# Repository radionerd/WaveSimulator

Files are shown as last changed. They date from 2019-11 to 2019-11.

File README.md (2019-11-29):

# Ship Motion Simulator

## Welcome

This is the repository for the Ship Motion Simulator design files

The design is contained in these folders:

* firmware   - Arduino .ino source file and status screenshot

* mechanical - LibreCAD drawings and templates - print the templates, glue on to mdf for cutting and drilling

* schematic  - EaglePCB schematics - also provided as pdf

* parts      - A list of all the purchased parts and where to get them

## Arrangement

The motion platform is controlled by an Arduino Nano mounted on the underside.

The Arduino Nano USB serial connection provides optional command line control and a status screen.

An optional plug in control panel provides convenient user controls using switches, potentiometers and a status LED.

## Background

The simulator was designed to approximate the pitch, roll and heave motions of a ship at sea using low cost model control servos.

For a more accurate simulation consider a Stewart Plaform with six degrees of freedom using linear actuators but higher cost and complexity.

The design was built and tested using the following software:

| Application | Version |
| --- | --- |
|  Arduino  | 1.8.9 |
|  EaglePCB | 8.3.1 |
|  LibreCAD | 2.1.2 |
|  Ubuntu | 18.04 |

## Photos and Videos

[Video](https://www.youtube.com/watch?v=MUajh_KlW8U) - Motion Research Ltd

[Construction Photos and Videos](https://photos.app.goo.gl/xF3chL2MP4UncZHGA)

## License

Copyright (C)2019 richard.jones.1952@gmail.com

[License GPL V3.0](https://www.gnu.org/licenses/gpl-3.0.en.html)

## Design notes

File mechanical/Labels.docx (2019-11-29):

Roll

Pitch

Heave

Period

Amplitude

USB USB USB USB

Panel

Auto

Manual

Motion Simulator

5V DC 5V DC

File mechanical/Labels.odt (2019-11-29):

Roll

Pitch

Heave

Period

Amplitude

USB

Panel

Auto

Manual

Motion Simulator

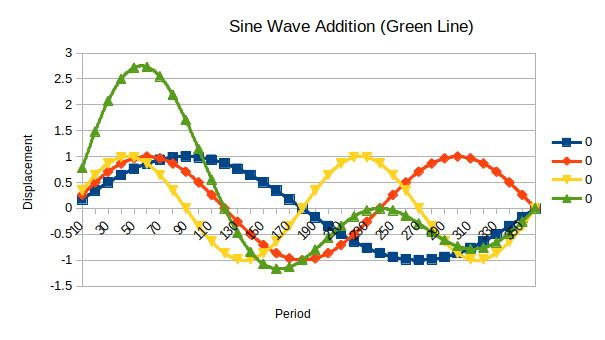
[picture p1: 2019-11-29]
firmware/SineWaveAddition.png

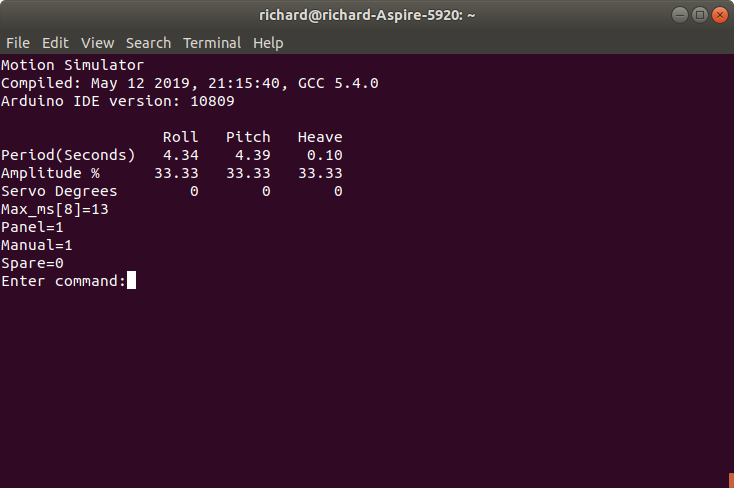
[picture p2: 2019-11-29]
firmware/Screenshot.png

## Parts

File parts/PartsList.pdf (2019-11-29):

### Sheet1

TotCost US$ | Cost NZ$ Order Qty | Description
2.56 USD | $3.97 Qty 2 ✔ | 20 way idc ribbon cable and 10x2 2.54mm connector
5.71 USD | $8.93 Qty 2 ws ✔ | Servo extension cable (wiring pots & switches)
1.71 USD | $2.68 Qty 1 ✔ | Double row header
2.73 USD | $4.27 Qty 1 ✔ | Double sided prototyping board
1.02 USD | $1.58 Qty 1 ✔ | M3 Hex Nuts
0.79 USD | $1.23 Qty 1 ✔ | M3 Washer
2.62 USD | $4.09 Qty 1 ✔ | Power Jacks
9.33 USD | $14.46 Qty 1 ✔ | M3 Ball joints
0.62 USD | $0.96 Qty 1 ✔ | Schottky Diodes to separate Servo 5v from USB
4.90 USD | $7.60 Qty 1 ws ✔ | 5V 3A AC Adapters
1.85 USD | $2.86 Qty 1 ✔ | Toggle Switches
3.99 USD | $6.19 Qty 1 ws ✔ | Metal Servo Wheel
4.96 USD | $7.69 Qty 1 ✔ | Arduino Nano
7.69 USD | $12.03 Qty 1 ✔ | 10k Sliding Pots
3.31 USD | $5.14 Qty 2 ✔ | 10k Rotary Pots
7.49 USD | $11.61 Qty 1 ✔ | M3x170mm threaded rod
26.45 USD | $40.93 Qty 1 ✔ | MG996 Servo Two spares
87.73 USD | $136.22 | Total to date

Part Count | Link
20 | https://www.aliexpress.com/item/-/32981928255.html?spm=a2g0o.cart.99999999.260.1ab93c007qi2Me
20 | https://www.aliexpress.com/item/-/32839590741.html?spm=a2g0o.cart.99999999.260.30453c00aDCjLZ
10 | https://www.aliexpress.com/item/10Pcs-2-54mm-2x40-Pin-80-Pin-Gold-Plated-Pitch-Male-Double-Row-Pin-Header-Strip/32856568534.html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
5 | https://www.aliexpress.com/item/10Pcs-Double-Side-5x7-cm-Prototype-Universal-FR-4-Glass-Fiber-PCB-Board/1852170278.html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
100 | https://www.aliexpress.com/item/Free-shipping-100pcs-lot-Metric-thread-DIN934-M3-304-Stainless-Steel-Hex-Nuts/32405600179.html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
100 | https://www.aliexpress.com/item/M2-M2-5-M3-M4-M5-M6-304-stainless-steel-flat-washer-thick-washers/32480666523.html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
(5) https://www.aliexpress.com/item/-/32845729569.html?spm=a2g0o.cart.99999999.260.72833c00aVzrED
(30) https://www.aliexpress.com/item/-/32945319578.html?spm=a2g0o.cart.99999999.267.72833c00aVzrED
(20) https://www.aliexpress.com/item/20PCS-1N5822-IN5822-40V-3A-SCHOTTKY-DIODE/32224138996.html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
(2) https://www.aliexpress.com/item/15W-AC-Converter-Adapter-5V-3A-Power-Supply-Charger-AU-plug-3000mA-MICRO-USB/32832175323.html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
(10) https://www.aliexpress.com/item/-/32907563794.html?spm=a2g0o.cart.99999999.287.72833c00aVzrED
(10) https://www.aliexpress.com/item/5pcs-1020F05-MG995-Metal-Servo-Arm-25T-Disc-Matal-Horns-for-MG995-MG996R-rc-Servos-Robot/1492767134.html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
(2) https://www.aliexpress.com/item/Free-Shipping-for-Arduino-Nano-V3-0-controller-ATMEGA328P-ATMEGA328-original-CH340-USB-cable/32607801066.html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
(6) https://www.aliexpress.com/item/-/32868946780.html?spm=a2g0o.cart.99999999.311.72833c00aVzrED
(10) https://www.aliexpress.com/item/-/32948875673.html?spm=a2g0o.cart.99999999.317.72833c00aVzrED
(10) https://www.aliexpress.com/item/-/32859175622.html?spm=a2g0o.cart.99999999.323.72833c00aVzrED
(8) https://www.aliexpress.com/item/MG996R-MG996-Metal-Gear-RC-Servo-High-Speed-Torque-RC-CAR-1-8/32355876966.html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

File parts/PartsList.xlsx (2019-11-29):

TotCost US$ | Cost NZ$ | Order Qty | Description | Part Count | Link
2.56 USD | $3.97 | Qty 2 ✔ | 20 way idc ribbon cable and 10x2 2.54mm connector | 20 | https://www.aliexpress.com/item/-/32981928255.html?spm=a2g0o.cart.99999999.260.1ab93c007qi2Me
5.71 USD | $8.93 | Qty 2 ✔ws | Servo extension cable (wiring pots & switches) | 20 | https://www.aliexpress.com/item/-/32839590741.html?spm=a2g0o.cart.99999999.260.30453c00aDCjLZ
1.71 USD | $2.68 | Qty 1 ✔ | Double row header | 10 | https://www.aliexpress.com/item/10Pcs-2-54mm-2x40-Pin-80-Pin-Gold-Plated-Pitch-Male-Double-Row-Pin-Header-Strip/32856568534.html
2.73 USD | $4.27 | Qty 1 ✔ | Double sided prototyping board | 5 | https://www.aliexpress.com/item/10Pcs-Double-Side-5x7-cm-Prototype-Universal-FR-4-Glass-Fiber-PCB-Board/1852170278.html
1.02 USD | $1.58 | Qty 1 ✔ | M3 Hex Nuts | 100 | https://www.aliexpress.com/item/Free-shipping-100pcs-lot-Metric-thread-DIN934-M3-304-Stainless-Steel-Hex-Nuts/32405600179.html
0.79 USD | $1.23 | Qty 1 ✔ | M3 Washer | 100 | https://www.aliexpress.com/item/M2-M2-5-M3-M4-M5-M6-304-stainless-steel-flat-washer-thick-washers/32480666523.html
2.62 USD | $4.09 | Qty 1 ✔ | Power Jacks | (5) | https://www.aliexpress.com/item/-/32845729569.html?spm=a2g0o.cart.99999999.260.72833c00aVzrED
9.33 USD | $14.46 | Qty 1 ✔ | M3 Ball joints | (30) | https://www.aliexpress.com/item/-/32945319578.html?spm=a2g0o.cart.99999999.267.72833c00aVzrED
0.62 USD | $0.96 | Qty 1 ✔ | Schottky Diodes to separate Servo 5v from USB | (20) | https://www.aliexpress.com/item/20PCS-1N5822-IN5822-40V-3A-SCHOTTKY-DIODE/32224138996.html
4.90 USD | $7.60 | Qty 1 ✔ws | 5V 3A AC Adapters | (2) | https://www.aliexpress.com/item/15W-AC-Converter-Adapter-5V-3A-Power-Supply-Charger-AU-plug-3000mA-MICRO-USB/32832175323.html
1.85 USD | $2.86 | Qty 1 ✔ | Toggle Switches | (10) | https://www.aliexpress.com/item/-/32907563794.html?spm=a2g0o.cart.99999999.287.72833c00aVzrED
3.99 USD | $6.19 | Qty 1 ✔ws | Metal Servo Wheel | (10) | https://www.aliexpress.com/item/5pcs-1020F05-MG995-Metal-Servo-Arm-25T-Disc-Matal-Horns-for-MG995-MG996R-rc-Servos-Robot/1492767134.html
4.96 USD | $7.69 | Qty 1 ✔ | Arduino Nano | (2) | https://www.aliexpress.com/item/Free-Shipping-for-Arduino-Nano-V3-0-controller-ATMEGA328P-ATMEGA328-original-CH340-USB-cable/32607801066.html
7.69 USD | $12.03 | Qty 1 ✔ | 10k Sliding Pots | (6) | https://www.aliexpress.com/item/-/32868946780.html?spm=a2g0o.cart.99999999.311.72833c00aVzrED
3.31 USD | $5.14 | Qty 2 ✔ | 10k Rotary Pots | (10) | https://www.aliexpress.com/item/-/32948875673.html?spm=a2g0o.cart.99999999.317.72833c00aVzrED
7.49 USD | $11.61 | Qty 1 ✔ | M3x170mm threaded rod | (10) | https://www.aliexpress.com/item/-/32859175622.html?spm=a2g0o.cart.99999999.323.72833c00aVzrED
26.45 USD | $40.93 | Qty 1 ✔ | MG996 Servo Two spares | (8) | https://www.aliexpress.com/item/MG996R-MG996-Metal-Gear-RC-Servo-High-Speed-Torque-RC-CAR-1-8/32355876966.html
87.73 USD | $136.22 |  | Total to date

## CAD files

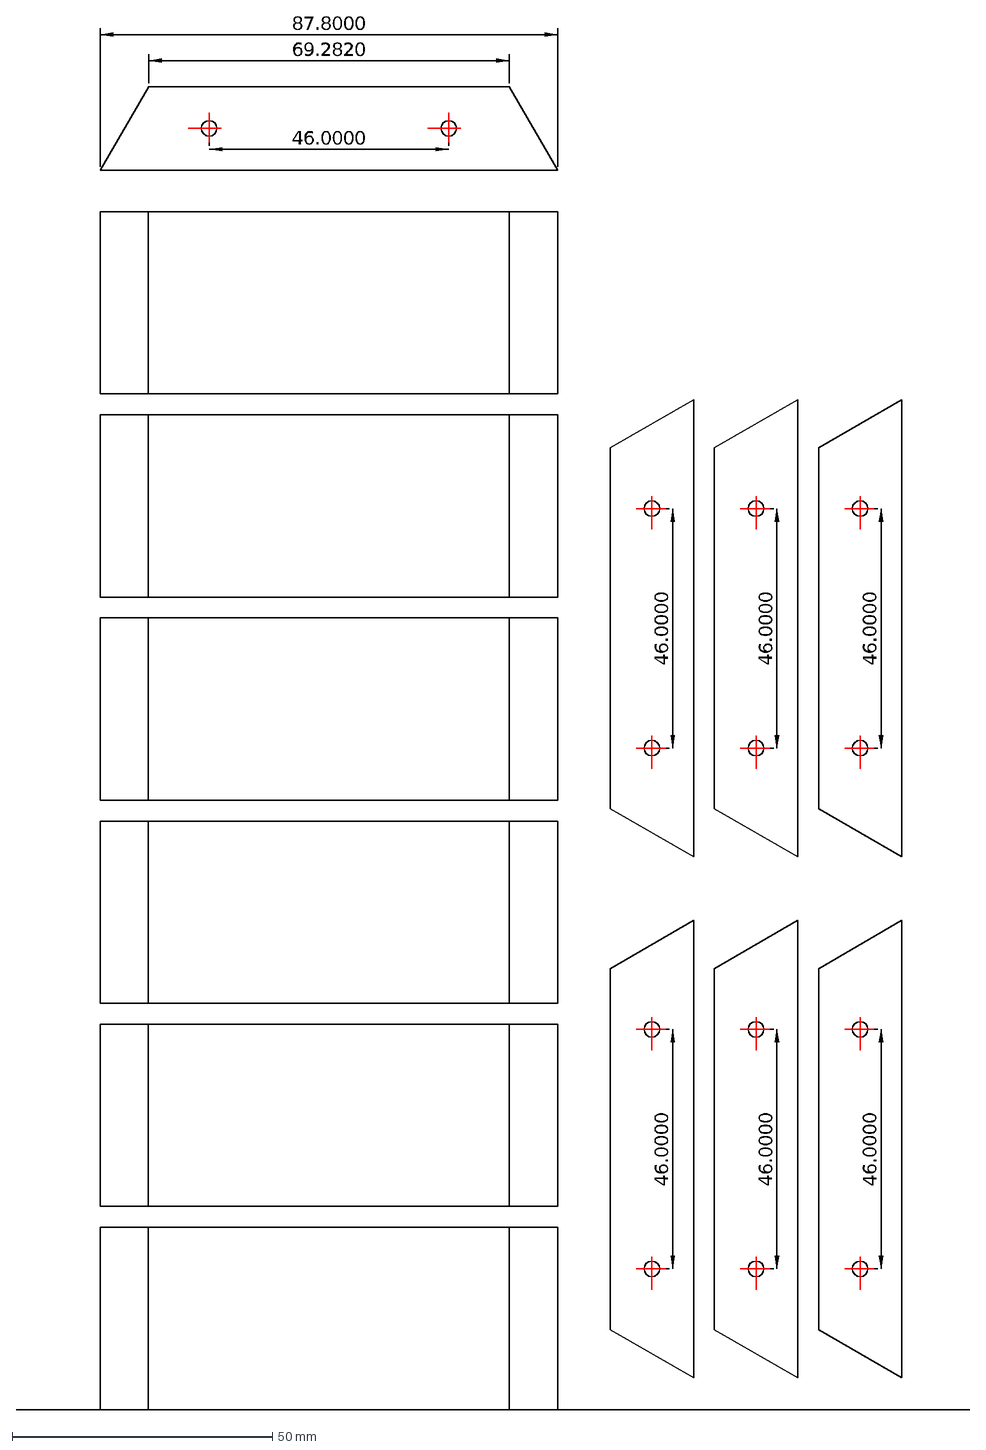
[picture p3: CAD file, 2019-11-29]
mechanical/PlatformWalls.dxf
46.0000
69.2820
87.8000

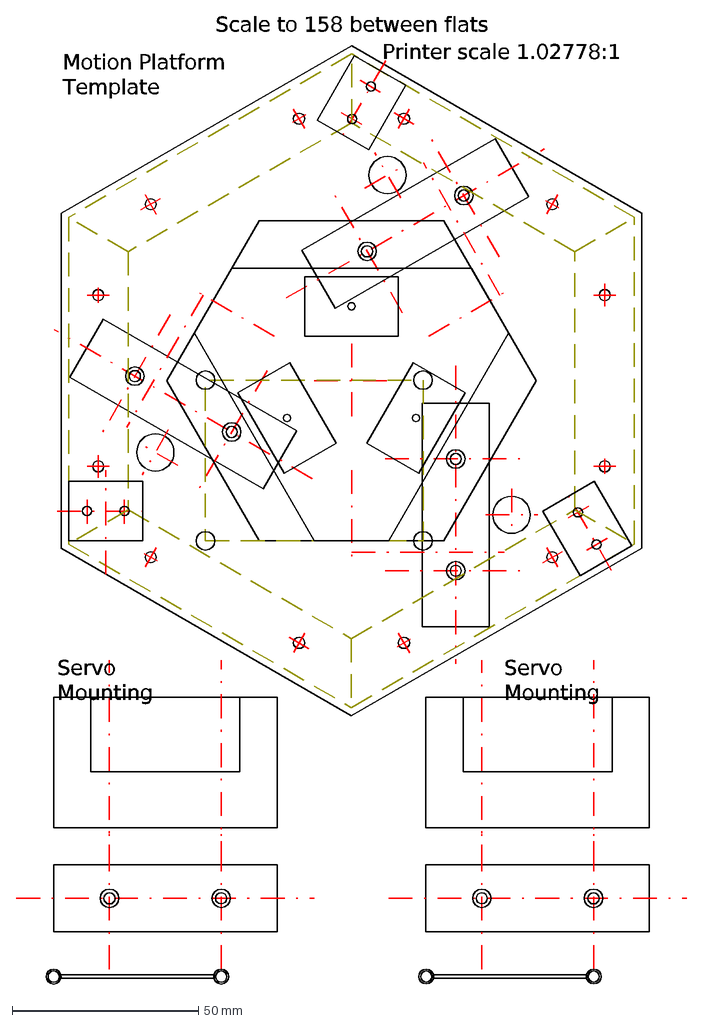
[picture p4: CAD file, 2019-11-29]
mechanical/PlatformHex.dxf
Scale to 158 between flats
Servo Mounting
Motion Platform Template
Printer scale 1.02778:1

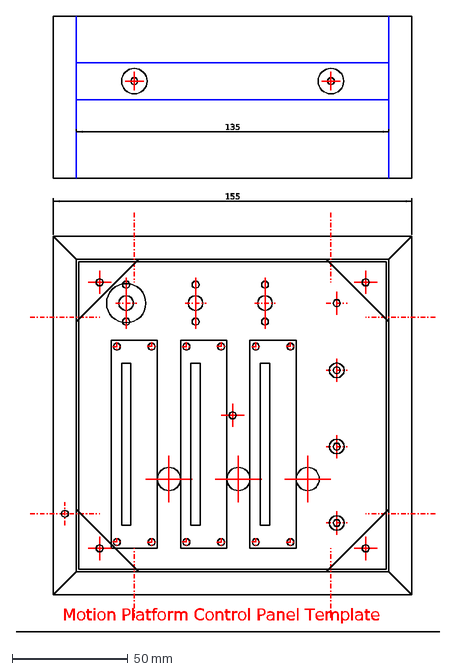
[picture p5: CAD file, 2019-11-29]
mechanical/ControlPanel.dxf
Motion Platform Control Panel Template
155
135

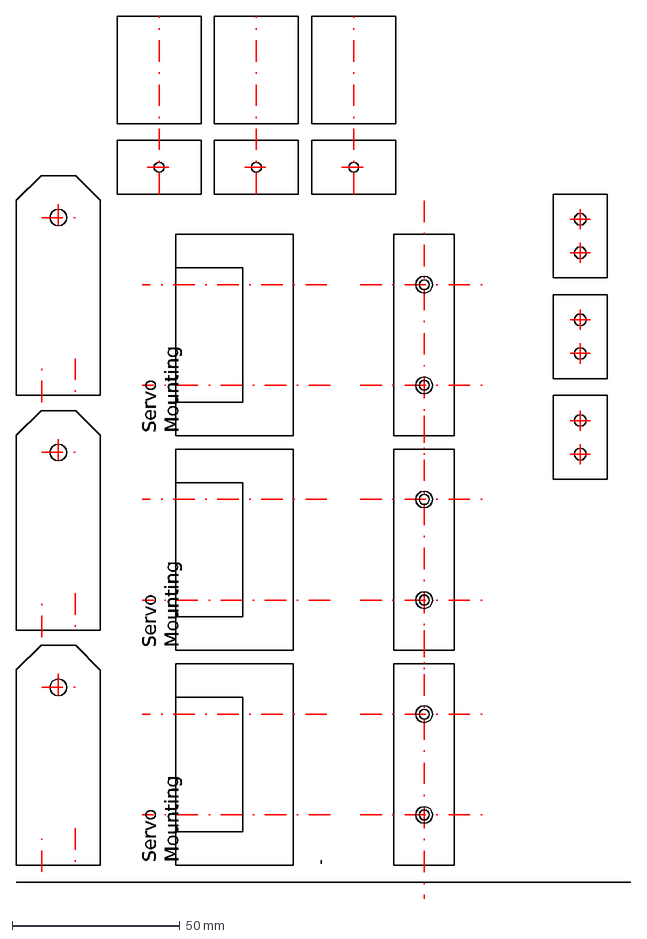
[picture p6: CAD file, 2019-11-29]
mechanical/PlatformTemplates.dxf
Servo Mounting

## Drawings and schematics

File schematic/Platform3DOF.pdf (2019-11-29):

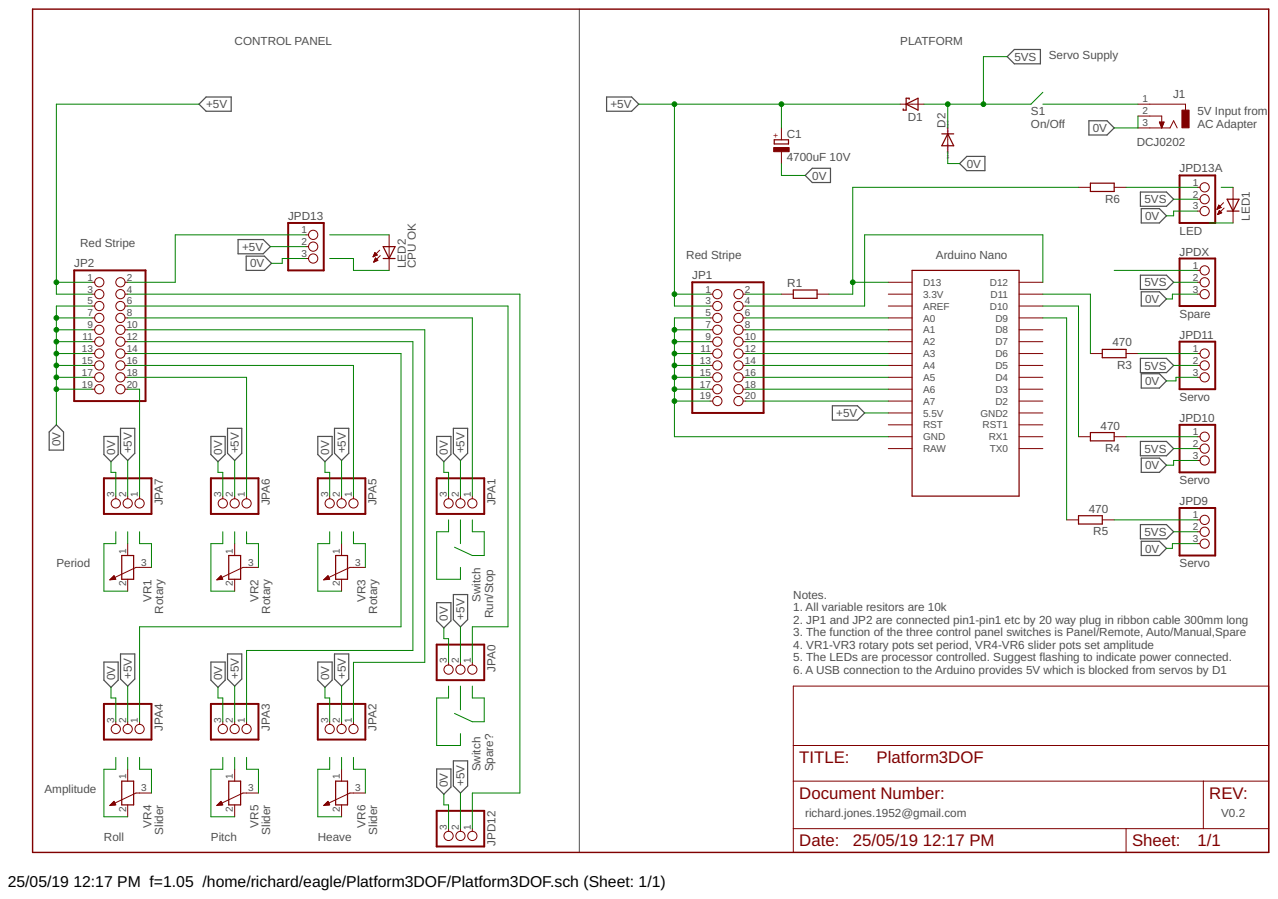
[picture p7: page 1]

Switch Spare? Switch Run/Stop

Notes. 1. All variable resitors are 10k
2. JP1 and JP2 are connected pin1-pin1 etc by 20 way plug in ribbon cable 300mm long
3. The function of the three control panel switches is Panel/Remote, Auto/Manual,Spare
4. VR1-VR3 rotary pots set period, VR4-VR6 slider pots set amplitude
5. The LEDs are processor controlled. Suggest flashing to indicate power connected. 6. A USB connection to the Arduino provides 5V which is blocked from servos by D1

Document Number: richard.jones.1952@gmail.com | REV: V0.2

Date: 25/05/19 12:17 PM | Sheet: 1/1

25/05/19 12:17 PM f=1.05 /home/richard/eagle/Platform3DOF/Platform3DOF.sch (Sheet: 1/1)

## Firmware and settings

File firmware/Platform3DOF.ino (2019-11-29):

  /*
   * Ships Motion Simulator
   *
   * Copyright (C)2019 richard.jones.1952@gmail.com
   *
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
   * This file contains embedded software to drive a 3 degrees of freedom motion simulator
   * The firmware was compiled and tested using Arduino v1.8.9 hosted on Ubuntu 18.04
   * The hardware is an Ardiuno Nano, pin out adapter, 3 servos and a control panel with 6 10k pots and 3 switches.
   * The similator may also be controlled over the serial USB link at 115200 baud using a VT100 terminal emulator. 
   * 
   */
#include <Servo.h>



const    int                NUM_SERVOS=3;
static float wave_period   [NUM_SERVOS] = { 9,10,11}; // seconds
static float wave_amplitude[NUM_SERVOS] = { 33.33,33.33,33.33}; // percent
static float wave_angle    [NUM_SERVOS]; // radians
static   int servo_position[NUM_SERVOS]; // degrees 0-180
Servo        servo         [NUM_SERVOS]; // create servo objects to control each servo
static unsigned task_number, max_ms, max_task; 
static bool manual_state, spare_state ;

// the setup function runs once when you press reset or power the board
void setup() {
  // Assign CPU i/o pins
  pinMode(LED_BUILTIN, OUTPUT); // initialize digital pin D13 LED_BUILTIN as an output.
  pinMode(12, INPUT_PULLUP ); // Control panel Run/Stop
  servo[0].attach(11); // servo output D11
  servo[1].attach(10); // servo output D10
  servo[2].attach( 9); // servo output D9
    // initialize serial communication
  Serial.begin(115200); // Baud rate
  char buffer[]={ 27,'[','2','J',0}; // VT100 Clear screen character sequence
  Serial.print(buffer); // Clear terminal emulator screen
}

// Flash the LED to show what a state we are in
void LEDUpdate()
{
  int led;
  int milliseconds = millis();
  int brightness = milliseconds &2047;
  if ( PanelEnabled() ) {
    // gentle fade led brightness, 2.048 second fade, 16ms pwm
    if ( brightness > 1023 ) brightness = 2047 - brightness;  // range 0-1023-0
    brightness = brightness >> 6; // now 0-15
    int pwm = milliseconds & 15;
    led = brightness <= pwm;
  } else {
    // hard flash led when panel disabled
    led = brightness > 1023;  
  }
  if ( led )
    digitalWrite(LED_BUILTIN, HIGH);   // turn the LED on (HIGH is the voltage level) 
  else
    digitalWrite(LED_BUILTIN, LOW);    // turn the LED off by making the voltage LOW
}



// the loop function runs over and over again forever
void loop() {
  unsigned long entry_time = millis(); // Get number of milliseconds since reset
  LEDUpdate();  
  switch (task_number) {
  // LoopTimer();   // Log loop time characteristics
    case 0: case 1: case 2: case 3 : case 4: case 5: case 6: case 7:
      PanelInput();  // Read the pots and switches on the panel and update if enabled
      break;
    case 8:
      SerialOutput();// Display an activity screen to a VT100 terminal emulator over USB
      break;
    case 9:
      SerialInput(); // Action serial commands sent over the USB connection, panel must turned off
      break;
    case 10:
      Motion();      // Update servo positions depending on run/manual mode
      break;
    default:
      task_number = -1;
  }
//  char buffer[80];
//  sprintf(buffer,"Return from task %d",task_number);
//  Serial.println(buffer);

  unsigned long elapsed_time = millis()-entry_time;
  if ( elapsed_time > max_ms ) {
    max_task = task_number;
    max_ms = elapsed_time;
  }
  task_number++;
}

bool PanelEnabled(void)
{
  return !digitalRead( 12 );
}

// Read potentiometer and switch inputs if enabled by D12
void PanelInput()
{
  int index;
  int channel = task_number & 7;
  if ( PanelEnabled() ) { // optional disable panel input for USB only control
    int val = analogRead( channel + A0 ); // Read one of 8 potentiometer inputs
    switch ( channel ) // Map analogue inputs to function
    {
    case 0: // Auto/Manual
      manual_state = val > 512;
      break;
    case 1: // spare
      spare_state = val > 512;
      break;
    case 2: case 3: case 4: // Slider pots
      index = 4 - channel;
      if ( manual_state ) {
        val = map(val, 0, 1023, 0, 180); // scale 0-180 degrees
        servo_position[index] = val;
      } else {
        float fval = val;
        fval = fval/10.23; // scale 0-100%
        wave_amplitude[index] = fval;
      }
      break;
    case 5: case 6: case 7: // Rotary pots
      index = 7 - channel;
      wave_period[index] = (float)val/50.0; // 0 to 20.47 seconds
      if ( wave_period[index] < 0.1 ) wave_period[index] = 0.1;
    }
  }
}

// Action serial commands sent over the USB connection, panel must turned off
// Build up a command line until \n received, allow bs/del for corrections
const   int INPUT_BUFFER_SIZE=81;
static char input_buffer[INPUT_BUFFER_SIZE];

void SerialInput(void)
{
  const char BELL=7;
  const char BACKSPACE=8;
  const char DELETE=0x7f;
  
  if (Serial.available() > 0) {
    char c = Serial.read();  //gets one byte from serial buffer
    unsigned len = strlen(input_buffer);
    switch ( c ) {
      case BACKSPACE :
      case DELETE :
        if ( len ) {
          input_buffer[ --len ] = 0;
          Serial.print("\010"); // backspace
        }
      break;
      case '\n' :
      case '\r' :
        DecodeCommand(input_buffer);
        input_buffer[0]=0; // clear input buffer
      break;
      default:
        if ( c >= ' ' ) {
          if ( len < ( sizeof(input_buffer)-2) ) {
            input_buffer[ len++ ] = c;
            input_buffer[ len ] = 0;
            Serial.print(c);
          } else {
            Serial.print(BELL);  
          }
        }
    }
  } 
}

// Display parameters on serial VT100 via USB at 1 second intervals
void SerialOutput()
{
  int i;
  char buffer[256];
  char home[] = {0x1b,'[','H',0}; // VT100 home string
  static unsigned long next_time;

  unsigned long now = millis();
  if ( next_time==0) {
    next_time = now+2000; // startup display
    Serial.print( F("Motion Simulator\r\n"));
    Serial.print( F("Compiled: "));
    Serial.print( F(__DATE__));
    Serial.print( F(", "));
    Serial.print( F(__TIME__));
    Serial.print( F(", GCC "));
    Serial.print( F(__VERSION__));
    Serial.print(F( "\r\nArduino IDE version: "));
    Serial.println( ARDUINO, DEC);
  }
  if ( now < next_time ) return ; // Print 1000ms intervals
  next_time = now + 1000;
  Serial.print(home);
  sprintf(buffer,"\r\n\n\n\n\t\t  Roll   Pitch   Heave");
  Serial.println(buffer);
  sprintf(buffer,"Period(Seconds)");
  Serial.print(buffer);
  buffer[0]='\t';
  for ( i = 0 ; i < NUM_SERVOS;i++) {
    dtostrf( wave_period[i] , 6, 2, buffer+1 );
    Serial.print(buffer);
  }
  Serial.println();
  sprintf(buffer,"Amplitude %%");
  Serial.print(buffer);
  buffer[0]='\t';
  for ( i = 0 ; i < NUM_SERVOS;i++) {
    dtostrf( wave_amplitude[i] , 6, 2, buffer+1 );
    Serial.print(buffer);
  }
//  Serial.println();
//  Serial.print(F("Wave Angle"));
//  buffer[0]='\t';
//  for ( i = 0 ; i < NUM_SERVOS;i++) {
//    dtostrf( wave_angle[i] , 6, 2, buffer+1 );
//    Serial.print(buffer);
//  }
  sprintf(buffer,"\r\nServo Degrees");
  Serial.print(buffer);
  for ( i = 0 ; i < NUM_SERVOS;i++) {
    sprintf(buffer,"\t%6d",servo_position[i]);
    Serial.print(buffer);
  }
  Serial.println();
  sprintf(buffer,"Max_ms[%d]=%2d\r\nPanel=%d\r\nManual=%d\r\nSpare=%d\r\n", max_task,max_ms,PanelEnabled(),manual_state,spare_state);
  Serial.print(buffer);
  Serial.print("Enter command:");
  Serial.print(input_buffer);
  Serial.print("\033[K"); // Clear to end of line
}

void DecodeCommand (char *buf ) {
  if ( PanelEnabled() ) {
    Serial.println("\n\rSwitch off control panel");
  }
  
  char cmd = toupper(buf[0]);
  int i=0;
  int var_idx=0;
  switch ( cmd )
  {
    case 'P' :
    case 'A' :
    case 'S' :
      while ( buf[i] && ( var_idx < NUM_SERVOS ) ) {
        i += strcspn( &buf[i] , ".0123456789" ); // locate number
        if ( buf[i] ) {
          if ( cmd == 'P' ) wave_period   [var_idx++] = atof( &buf[i] );
          if ( cmd == 'A' ) wave_amplitude[var_idx++] = atof( &buf[i] );
          if ( cmd == 'S' ) servo_position[var_idx++] = atof( &buf[i] );
        }
        i += strcspn( &buf[i] , " " ); // pass over previous number       
      }      
    break;
    case 'M' : // Manual = 0/1
      i = strcspn( buf , "01" );
      if ( buf[i] != 0 )
        manual_state = buf[i] & 1;
      break;
  }
}
//static float wave_period   [NUM_SERVOS]; // seconds
//static float wave_amplitude[NUM_SERVOS]; // percent
//static float wave_angle    [NUM_SERVOS]; // radians
//static   int servo_position[NUM_SERVOS]; // degrees 0-180

// Update servo positions @ 40Hz i.e. every 25ms
void Motion()
{
  static unsigned long next_time;
  const float sample_freq = 40.0; // 40.0Hz
  const int sample_rate_ms = 1000/sample_freq;
  const float pi = 3.1415926;
  float wave_height [NUM_SERVOS];
  int i;

  unsigned long now = millis();
  // if ( next_time==0) next_time = now; // set startup condition
  if ( now < next_time ) return ; // 
  next_time = now + sample_rate_ms; // Update servos at 25 ms intervals for precise rate control in auto
  if ( ! manual_state ) {
    // Auto mode
    // update waves for roll, pitch and heave
    // Assumptions:
    // 1. Wave motions are sinusoidal
    // 2. Wave in different directions add linearly
    // 3. The servo angular displacements translate linearly through the linkeage to the platform (they don't)
    // 4. To avoid limiting, the amplitude for each servo should be set no more than 33%
    // Nevertheless these assumptions are a handy first approximation
    for ( i = 0 ; i < NUM_SERVOS ; i++ ) {
      if ( wave_period[i] < 0.1 ) wave_period[i] = 0.1; // prevent divide by zero errors
      wave_angle[i] += (2*pi)/(wave_period[i]*sample_freq);
      if ( wave_angle[i] > 2*pi ) wave_angle[i] -= 2*pi;
      wave_height[i] = sin( wave_angle[i] ) * wave_amplitude[i] / 100.0; // range at 100% +/-1
    }
    const int roll=0, pitch=1,heave=2;
    const int left=0,centre=1,right=2;
    // map waves onto servo positions:
    //  Servo0  Servo2:
    //   Left    Right
    //     Servo1
    //     Centre
    servo_position[left]   = ((+wave_height[roll]+wave_height[pitch]+wave_height[heave])*90.0)+90;
    servo_position[centre] = ((                  -wave_height[pitch]+wave_height[heave])*90.0)+90;
    servo_position[right]  = ((-wave_height[roll]+wave_height[pitch]+wave_height[heave])*90.0)+90;
  }
  // Update servo positions
  for ( i = 0 ; i < NUM_SERVOS ; i++ ) {
    //if ( servo_position[i] <  0 ) servo_position[i] =   0;
    //if ( servo_position[i] >180 ) servo_position[i] = 180;   
    servo[i].write(servo_position[i]);
  }
}

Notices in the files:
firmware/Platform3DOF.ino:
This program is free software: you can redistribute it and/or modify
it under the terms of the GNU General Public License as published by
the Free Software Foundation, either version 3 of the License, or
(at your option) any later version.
